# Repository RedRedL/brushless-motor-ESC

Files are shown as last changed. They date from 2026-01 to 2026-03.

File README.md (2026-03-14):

<br />
<div align="center">
  <a href="https://github.com/RedRedL/brushless-motor-ESC">
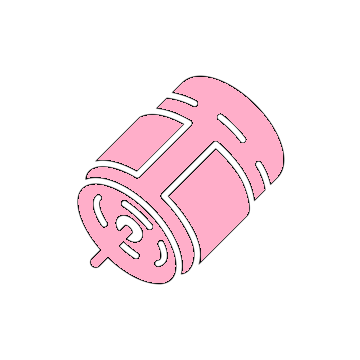
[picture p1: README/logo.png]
    
  </a>
  <h3 align="center">Simple Brushless Motor Electronic Speed Controller</h3>

  <p align="center">
    A simple BLDC ESC with RC PWM control built on perfboard.
  </p>
</div>

## About The Project

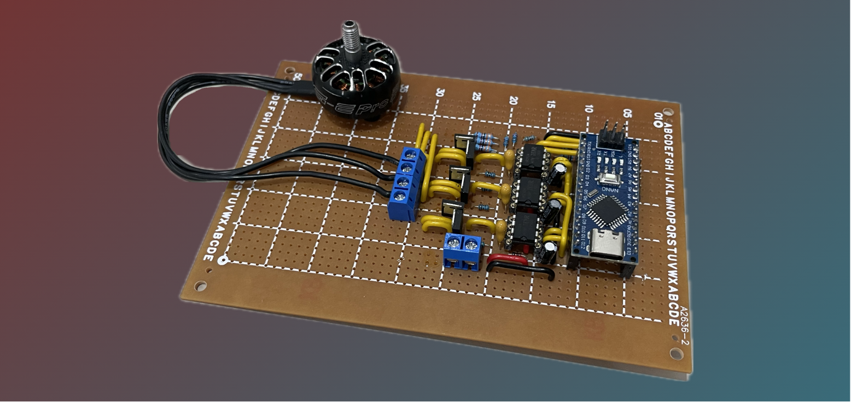
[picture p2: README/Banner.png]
ESC Banner


This project started with my naivety and ignorance. In an effort to avoid buying an ESC for my RC plane, I went down a rabbit hole learning how to build one and ultimately discovered why just buying one would have saved me a lot of time (lol).

While trying to understand how a BLDC ESC works, I found many existing projects either too confusing or too advanced for my skill level. That’s why I decided to build my own barebones ESC as a clear, beginner-friendly learning project to figure out how this stuff actually works.

## Schematic
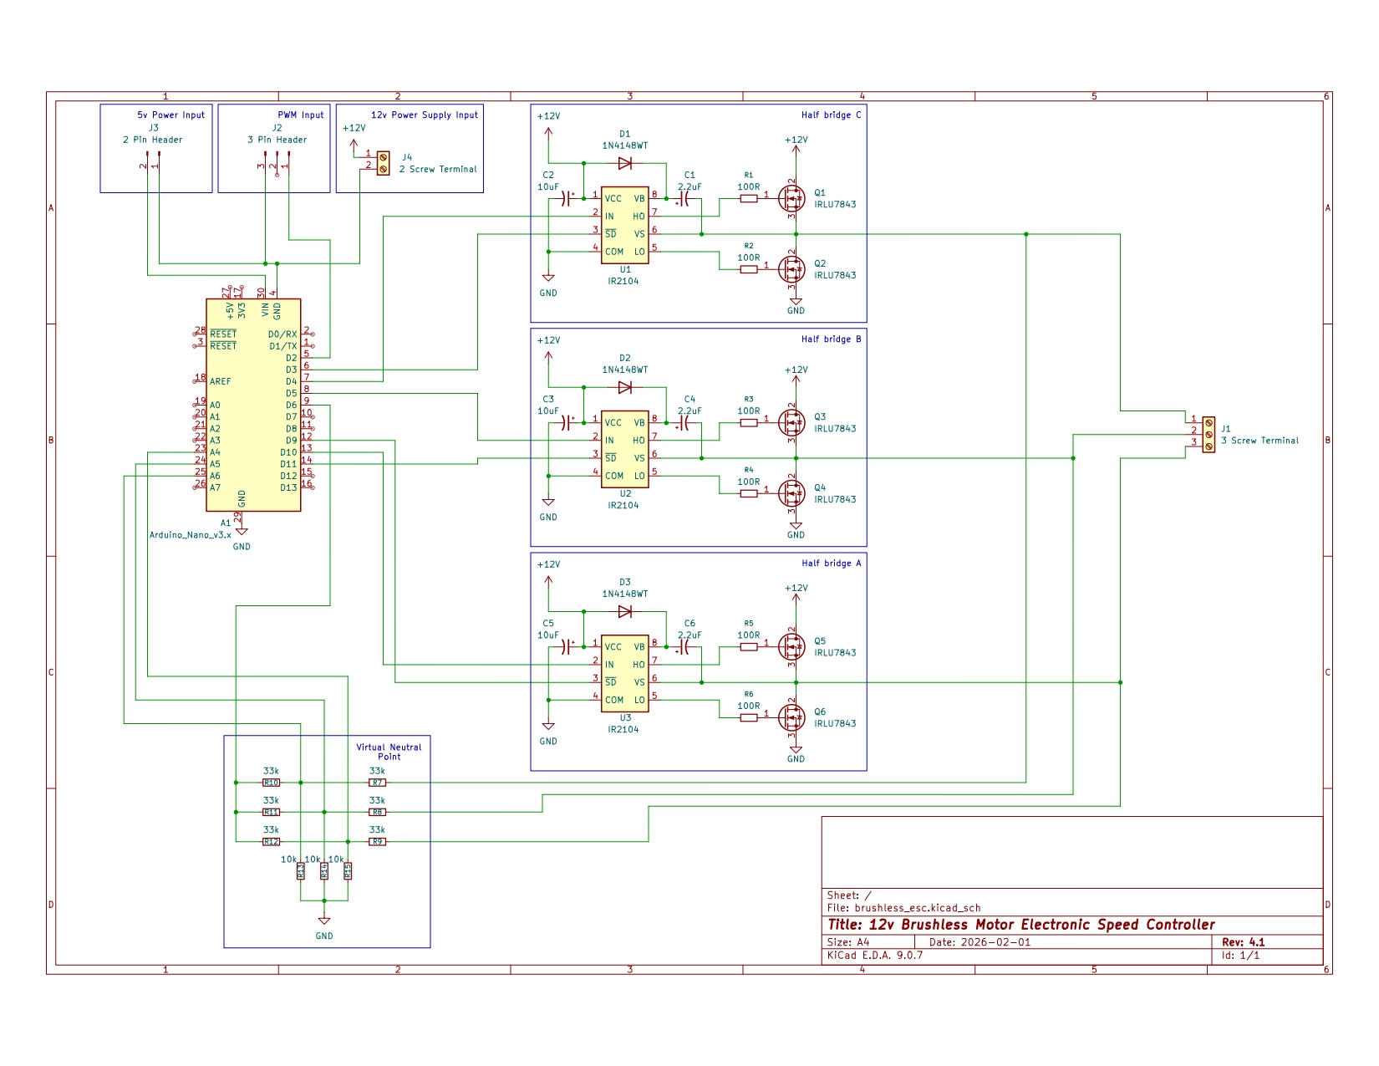
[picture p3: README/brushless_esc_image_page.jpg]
Schematic


## Video

<video src="https://github.com/user-attachments/assets/7b0f5fe2-bafd-46f4-bc8f-bd8ba11c937b" controls></video>

### Bill of Materials

Most of this stuff I bought from Aliexpress (cause im broke)

* Arduino Nano 3.0
* 3x IR2104
* 6x IRLU7843
* 3x 2.2uF Tantalum capacitor
* 3x 10uF Electrolytic Capacitor
* 3x 1N4148 Diode
* 6x 33k Resistor
* 3x 10k Resistor
* 6x 100R Resistor
* 22 AWG Solidcore Wire
* Perfboard
* Headers
* Screw Terminals

### Tools I used

* Multimeter (Ferrex, ALDI)
* Soldering Iron (FNIRSI HS-02)
* Oscilloscope (Rigol DHO804)
* Power Supply (Korad KA3005DS)

## License

Distributed under the Unlicense License. See `LICENSE.txt` for more information.

## Contact

Red - Redstbox@proton.me

## Acknowledgments

As a total beginner this project would not be possible without these resources (and people!)

* [Port Manipulation](https://docs.arduino.cc/retired/hacking/software/PortManipulation/)
* [Arduino Language Reference](https://docs.arduino.cc/language-reference/en/functions/math/map/)
* [Foolish Engineer Bootstrap Gate driving circuit](https://www.youtube.com/watch?v=em5BuCFSuBw&t)
* [Simple Circuits ESC](https://simple-circuit.com/arduino-brushless-dc-motor-controller/)
* [HyperSpace Pirates ESC](https://www.youtube.com/watch?v=F8l9Z1HGYcU)
* [ReadMe Layout](https://github.com/othneildrew/Best-README-Template/tree/main)

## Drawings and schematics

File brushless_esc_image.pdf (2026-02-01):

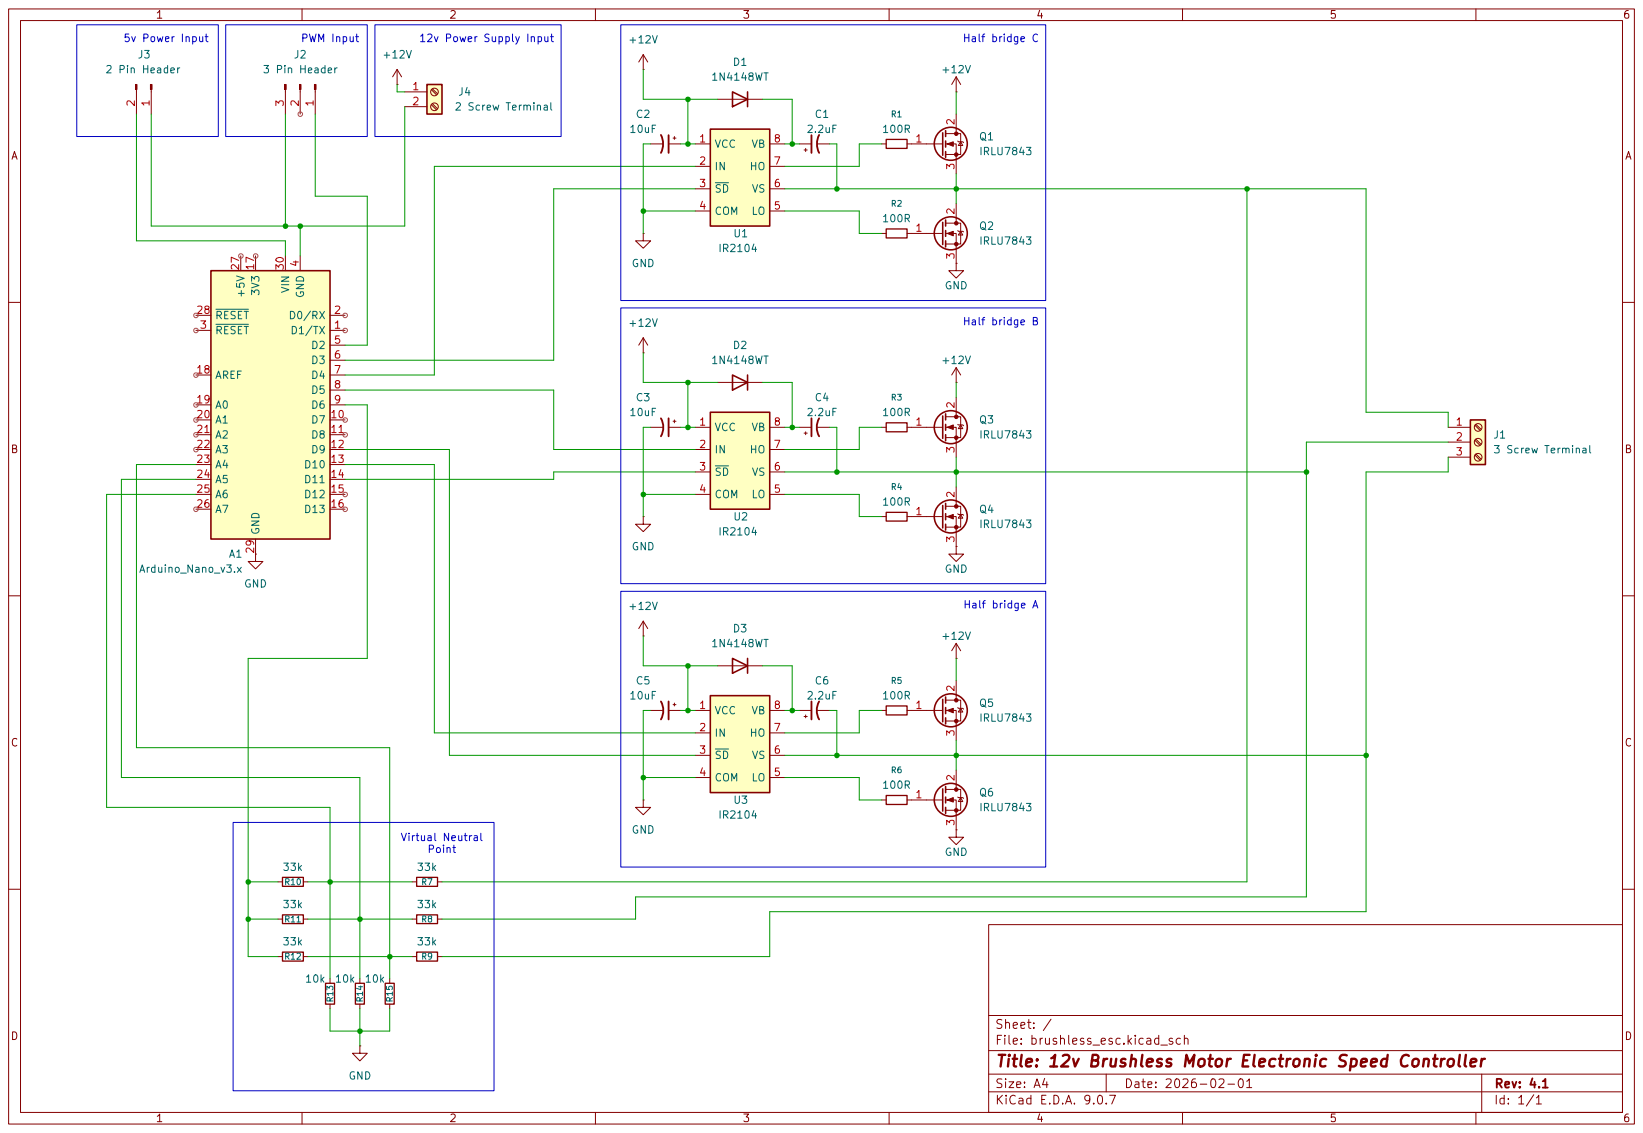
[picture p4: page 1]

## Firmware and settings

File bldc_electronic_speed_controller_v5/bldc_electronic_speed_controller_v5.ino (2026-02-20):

/*
Author: RedRedL
Creation Date: 13/01/2026
Version: 6.0
References:
  [https://docs.arduino.cc/retired/hacking/software/PortManipulation/](https://docs.arduino.cc/retired/hacking/software/PortManipulation/)
  [https://ww1.microchip.com/downloads/en/DeviceDoc/Atmel-7810-Automotive-Microcontrollers-ATmega328P_Datasheet.pdf](https://ww1.microchip.com/downloads/en/DeviceDoc/Atmel-7810-Automotive-Microcontrollers-ATmega328P_Datasheet.pdf)
  [https://docs.arduino.cc/language-reference/en/functions/math/map/](https://docs.arduino.cc/language-reference/en/functions/math/map/)
  [https://simple-circuit.com/arduino-brushless-dc-motor-controller/](https://simple-circuit.com/arduino-brushless-dc-motor-controller/)
  [https://www.youtube.com/watch?v=F8l9Z1HGYcU](https://www.youtube.com/watch?v=F8l9Z1HGYcU)
*/

#define THROTTLE 2

const byte MAX_PWM_DUTY = 255;
const byte MIN_PWM_DUTY = 50;
const byte DEACTIVATION_THRESHHOLD = 5;
volatile byte bldc_state = 0;

volatile bool motorActive = false;

volatile long unsigned int signalStart = 0;
volatile long unsigned int signalEnd = 0;
volatile long unsigned int signalLength = 0;
volatile byte pendingDutyValue = 50;

void pwm_reading_interrupt() {
  int isHigh = digitalRead(THROTTLE);
  if (isHigh) {
    signalStart = micros();
  } else {
    signalEnd = micros();
    update(); 
  }
}

void update() {
  signalLength = signalEnd - signalStart;

  if (signalLength < 900 || signalLength > 2100) {
    pendingDutyValue = 0;
    return;
  }

  int pwmValue = map(signalLength, 1000, 2000, 0, 255);
  pendingDutyValue = constrain(pwmValue, 0, 255);
  }

void adjust_pwm(int duty) {
  if (duty < MIN_PWM_DUTY)
    duty = MIN_PWM_DUTY;
  else if (duty > MAX_PWM_DUTY)
    duty = MAX_PWM_DUTY;
  OCR1A = duty;
  OCR2A = duty;
  OCR2B = duty;
}


void disable_driver_pins() {
  PORTB &= ~((1 << PB1) | (1 << PB2) | (1 << PB3));
  PORTD &= ~((1 << PD4) | (1 << PD3) | (1 << PD5));
  TCCR1A &= ~(1 << COM1A1);
  TCCR2A &= ~((1 << COM2A1) | (1 << COM2B1));
  }


void bldc_next(byte bldc_state) {
  switch(bldc_state){
    /*
    Driver A: SD -> TCCR1A::COM1A1 -> PORTB::PB1; IN -> PORTB::PB2
    Driver B: SD -> TCCR2A::COM2A1 -> PORTB::PB3; IN -> PORTD::PD5
    Driver C: SD -> TCCR2A::COM2B1 -> PORTD::PD3; IN -> PORTD::PD4
    */
    case 0: // Driver A is high, Driver B is low.
      disable_driver_pins();
      // Enable PWM on Driver A, set IN high
      TCCR1A |= (1 << COM1A1);
      PORTB |= (1 << PB2);  // IN high for Driver A
      PORTB |= (1 << PB3);  // SD high for Driver B (but PWM disabled)
      ADMUX = 6;
      ACSR |= (1 << ACIS1) | (1 << ACIS0);
      break;
    case 1: // Driver A is high, Driver C is low.
      disable_driver_pins();
      TCCR1A |= (1 << COM1A1);
      PORTB |= (1 << PB2);  // IN high for Driver A
      PORTD |= (1 << PD3);  // SD high for Driver C
      ADMUX = 5;
      ACSR &= ~(1 << ACIS0);
      break;
    case 2: // Driver B is high, Driver C is low.
      disable_driver_pins();
      TCCR2A |= (1 << COM2A1);
      PORTD |= (1 << PD5);  // IN high for Driver B
      PORTD |= (1 << PD3);  // SD high for Driver C
      ADMUX = 4;
      ACSR |= (1 << ACIS1) | (1 << ACIS0);
      break;
    case 3: // Driver B is high, Driver A is low.
      disable_driver_pins();
      TCCR2A |= (1 << COM2A1);
      PORTD |= (1 << PD5);  // IN high for Driver B
      PORTB |= (1 << PB1);  // SD high for Driver A
      ADMUX = 6;
      ACSR &= ~(1 << ACIS0);
      break;
    case 4: // Driver C is high, Driver A is low.
      disable_driver_pins();
      TCCR2A |= (1 << COM2B1);
      PORTD |= (1 << PD4);  // IN high for Driver C
      PORTB |= (1 << PB1);  // SD high for Driver A
      ADMUX = 5;
      ACSR |= (1 << ACIS1) | (1 << ACIS0);
      break;
    case 5: // Driver C is high, Driver B is low.
      disable_driver_pins();
      TCCR2A |= (1 << COM2B1);
      PORTD |= (1 << PD4);  // IN high for Driver C
      PORTB |= (1 << PB3);  // SD high for Driver B
      ADMUX = 4;
      ACSR &= ~(1 << ACIS0);
      break;
  }
}


void setup() {
  // Use port manipulation to assign pins.
  // Set pins 4, 3 and 5 to output
  DDRD = (1 << PD5) | (1 << PD3) | (1 << PD4); // PD5,4,3 is D5,4,3
  // Set pins 4, 3, 5 low
  PORTD = 0;
  // Set pins 9, 10 and 11 to output
  DDRB = (1 << PB3) | (1 << PB2) | (1 << PB1); // PB3-1 is D11-9
  // Set pins 9, 10 and 11 low
  PORTB = 0;


  TCCR1A = (1 << WGM10);  // Fast PWM mode 14
  TCCR1B = (1 << CS10);  // No prescaler
  // Timer2 setup (8-bit PWM on pins 3 and 11)
  TCCR2A = (1 << WGM20);  // Fast PWM mode 3
  TCCR2B = (1 << CS20);  // No prescaler


  // Analog comparator setting
  ACSR = (1 << ACI);   // Disable analog comparator initially
  ADCSRA = (0 << ADEN);  // Disable ADC
  ADCSRB = (1 << ACME);  // Enable ADC multiplexer for comparator
  // Set initial state and PWM
  adjust_pwm(100);  // Set PWM to 50/255

  pinMode(THROTTLE, INPUT);
  attachInterrupt(digitalPinToInterrupt(THROTTLE), pwm_reading_interrupt, CHANGE);
  pinMode(LED_BUILTIN, OUTPUT);
}



// Analog comparator ISR
ISR (ANALOG_COMP_vect) {
  // BEMF debounce
  for(int i = 0; i < 10; i++) {
    if(bldc_state & 1){
      if(!(ACSR & 0x20)) i -= 1;
    }
    else {
      if((ACSR & 0x20))  i -= 1;
    }
  }
 
  bldc_next(bldc_state);
  bldc_state++;
  bldc_state %= 6;
}

void start() {
  digitalWrite(LED_BUILTIN, HIGH);
  bldc_state = 0;
  adjust_pwm(100);

  for (int i = 5000; i > 100; i -= 20) {
    delayMicroseconds(i);
    bldc_next(bldc_state);
    bldc_state++;
    bldc_state %= 6;
  }
  motorActive = true;
  ACSR |= (1 << ACIE);  
}

void stop() {
  motorActive = false;
  disable_driver_pins();
  ACSR &= ~(1 << ACIE);
  digitalWrite(LED_BUILTIN, LOW);
}

void loop() {
  if (!motorActive && pendingDutyValue > MIN_PWM_DUTY) 
    start();
  
  if (motorActive && pendingDutyValue < DEACTIVATION_THRESHHOLD)
    stop();

  if (motorActive) 
    adjust_pwm(pendingDutyValue);
  
  }

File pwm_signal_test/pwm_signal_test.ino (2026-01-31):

#define THROTTLE 2

volatile long unsigned int signalStart = 0;
volatile long unsigned int signalEnd = 0;
volatile long unsigned int signalLength = 0;

void pwm_reading_interrupt() {
  int isHigh = digitalRead(THROTTLE);
  if (isHigh) {
    signalStart = micros();
  } else {
    signalEnd = micros();
    update(); 
  }
}

void update() {
  signalLength = signalEnd - signalStart;
  Serial.print(signalLength);

  int pwmValue = map(signalLength, 1000, 2000, 0, 255);
  int dutyValue = constrain(pwmValue, 0, 255);
  
  Serial.print(" ");
  Serial.println(dutyValue);
}

void setup() {
  Serial.begin(9600);
  pinMode(THROTTLE, INPUT);
  attachInterrupt(digitalPinToInterrupt(THROTTLE), pwm_reading_interrupt, CHANGE);
}

void loop() {
  // Your main code here
}

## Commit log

2026-01-31 Add test script to verify PWM signal reading
2026-02-01 Add reading for PWM RC controller to adjust DUTY cycle.
2026-02-01 Delete BLDC_ESC_V1 directory
    Rename
2026-02-01 Add schematic
    [brushless_esc.kicad_sch]
2026-02-01 Delete BLDC_ESC_V1.ino
    Merge with main
2026-02-01 Update and rename brushless_esc.kicad_sch to brushless_esc_schematic.kicad_sch
    [brushless_esc_schematic.kicad_sch]
2026-02-01 Add brushless_esc schematic image
2026-02-01 Finalised script with PWM control
2026-02-20 Modify pin assignments for Driver A and Driver C
    Updated pin assignments for Driver A and Driver C.
